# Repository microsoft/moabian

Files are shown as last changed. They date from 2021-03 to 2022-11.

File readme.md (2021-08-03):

# Welcome to Project Moab

Project Moab is an open source ball balancing robot built to demonstrate the end-to-end Microsoft Project Bonsai Platform, a low-code AI platform for building autonomous systems.

If you have the hardware kit, you can find all the setup documentation in the [Wiki](https://github.com/microsoft/moabian/wiki).

You can find an introduction to Autonomous systems and an overview of the Project Bonsai platform [here](https://innovation.microsoft.com/en-us/exploring-autonomous-systems).

For step-by-step tutorials of how to train a brain to balance a ball on Moab, visit the [Project Moab Website](https://microsoft.github.io/moab/).

Simulation is a huge component of Project Bonsai. You can find the python simulator for Project Moab [here](https://github.com/microsoft/moabsim-py). This is also where you can find the inkling files for the Project Moab tutorials.

There is also a MathWorks Project Moab simulation. You can find the Simulink and Simscape Multibody model [here](https://github.com/microsoft/bonsai-simulink/tree/main/samples/moab). Connecting this simulation to Project Bonsai requires the [Microsoft Project Bonsai Simulink Toolbox](https://www.mathworks.com/matlabcentral/fileexchange/75512-microsoft-project-bonsai-simulink-toolbox).

## Microsoft Open Source Code of Conduct

This project has adopted the [Microsoft Open Source Code of Conduct](https://opensource.microsoft.com/codeofconduct/).
For more information see the [Code of Conduct FAQ](https://opensource.microsoft.com/codeofconduct/faq/) or
contact [opencode@microsoft.com](mailto:opencode@microsoft.com)
with any additional questions or comments.

https://opensource.microsoft.com/codeofconduct

## Trademark Notice

Trademarks This project may contain trademarks or logos for projects,
products, or services. Authorized use of Microsoft trademarks or logos
is subject to and must follow Microsoft's Trademark & Brand Guidelines.
Use of Microsoft trademarks or logos in modified versions of this
project must not cause confusion or imply Microsoft sponsorship. Any use
of third-party trademarks or logos are subject to those third-party's
policies.

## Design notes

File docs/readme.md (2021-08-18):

# Getting started with Project Moab

### Power on

Connect Moab to an electrical outlet using the provided power supply.
The bot will automatically boot and display “PROJECT MOAB” when booting.
This can take up to a minute if Moab is not connected to internet. 

### Balance a ball

1. **Joystick Mode**

   Navigate to and select "JOYSTICK" mode by presssing the joystick. The plate will
   rise up and now you can manually control the pitch and roll of the
   plate using the joystick. Place the ping pong ball on the plate and
   try balancing the ball manually! 

   To exit Joystick mode, select the menu button next to the joystick.

2. **PID Mode**

    This is a PID (Proportional, Integral, Derivative) controller
    that balance the ball at the center of the plate. This controller
    works by minimizing the error between the actual ball position and
    velocity, and the desired ball position and velocity. This type of
    controller is the most commonly found in industrial control
    applications. This controller has been tuned specifially for the ping pong ball.

    Move the joystick down and select "PID" mode. Place the orange
    ping pong ball on the plate and watch Moab automatically balance
    the ball. Try disturbing the ball by poking it or blowing on it and
    watch Moab return the ball to the center.

    If Moab is unable to balance a ball or making erratic movements, see [Troubleshooting](https://github.com/microsoft/moabian/blob/main/docs/troubleshooting.md).

    To exit PID mode, select the menu button next to the joystick.

3. **Brain Mode**

    This is a brain that has been trained using the Bonsai platform. The
    brain is a neural network that has been trained using two goals:
    prevent the ball from falling off the plate, and balance the ball at
    the center of the plate. For details of how this brain was trained, see [Moab Tutorial 2](https://microsoft.github.io/moab/tutorials/2-robustness/index.html).

     Move the joystick down and select "BRAIN" mode. Place the orange
     ping pong ball on the plate and watch Moab automatically balance
     the ball. Try disturbing the ball by poking it or blowing on it and
     watch Moab return the ball to the center.

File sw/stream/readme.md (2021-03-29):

pip3 install --user requirements.txt
python3 app.py

-or-

gunicorn --threads 5 --works 1 --bind 0.0.0.0:8080 app:app

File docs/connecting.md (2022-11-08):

# Connecting to Moab

To deploy your own brain on Moab, you will need to connect to it on your
local network. For the initial setup, we recommend using an ethernet
cable to connect your Moab to your local network. If you are unable to
connect to your network with an ethernet cable you can do so using WiFi.
To configure the WiFi on your Moab, you will need an HDMI monitor and
USB keyboard.

## Option 1: Connecting with an ethernet cable

### Required Materials

- Ethernet cable (to connect Moab to your local network)

Connect one end of an ethernet cable to your Moab and the other end to
your router.

## Option 2: Connecting with an HDMI monitor and USB keyboard

### Required Materials

- HDMI Monitor
- USB Keyboard

1. Connect Moab to a monitor using an HDMI cable.

2. Connect Moab to a USB keyboard.

3. When prompted for the moab login, use "pi" and "raspberry":

    login: pi
    password: raspberry

4. Follow the instructions in the next section to enable the WiFi.

## Enable WiFi (required for Option 2)

1. Type `sudo raspi-config`, and hit enter to open the Raspberry Pi
Software Configuration Tool.

    >sudo raspi-config

2. If prompted, select your country from the list. You can type the
first letter of your country as a short cut.

3. Select **1 System Options**.

4. Select **S1 Wireless LAN**.

5. Enter your WiFi network name.

6. Enter your WiFi password.

7. Select **Finish**.

## SSH into Moab

There are multiple methods to SSH into Moab. We provide instructions for
using Visual Studio Code.

#### SSH into Moab using Visual Studio Code

1. Open Visual Studio Code. If you don't have it you can download it for
free [here](https://code.visualstudio.com/).

2. Add the extension **Remote - SSH**, if you don't already have it.
Click on the Extensions icon on the left, and search "Remote - ssh" as
shown in the following example. Click **Install**.

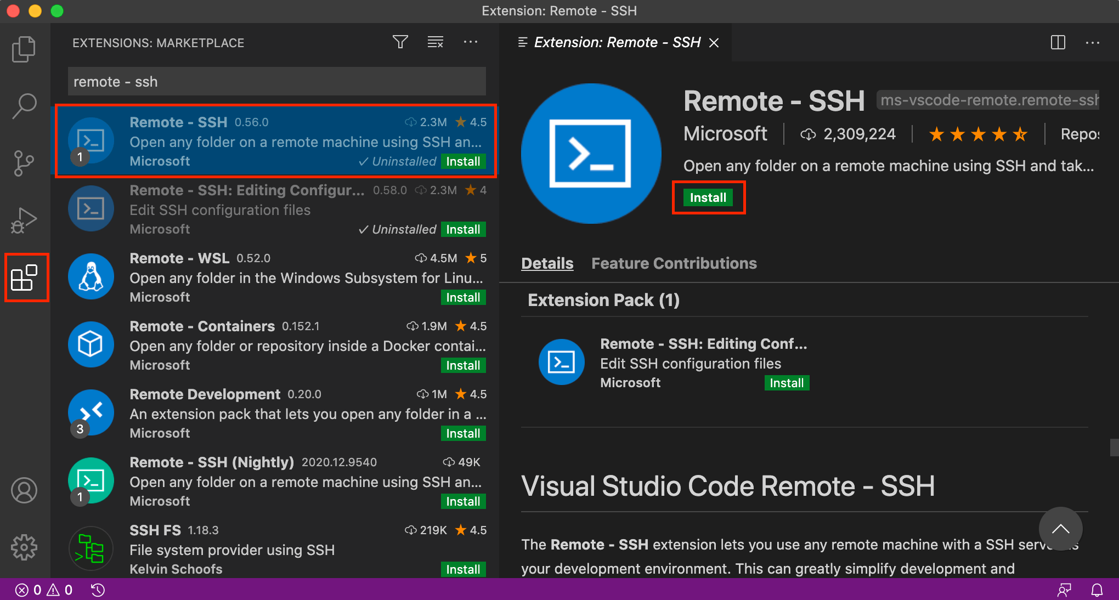
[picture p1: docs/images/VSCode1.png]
VSCode1
   

3. Add a new SSH host. Open the Command Palette through the **View**
menu as shown in the following screenshot:

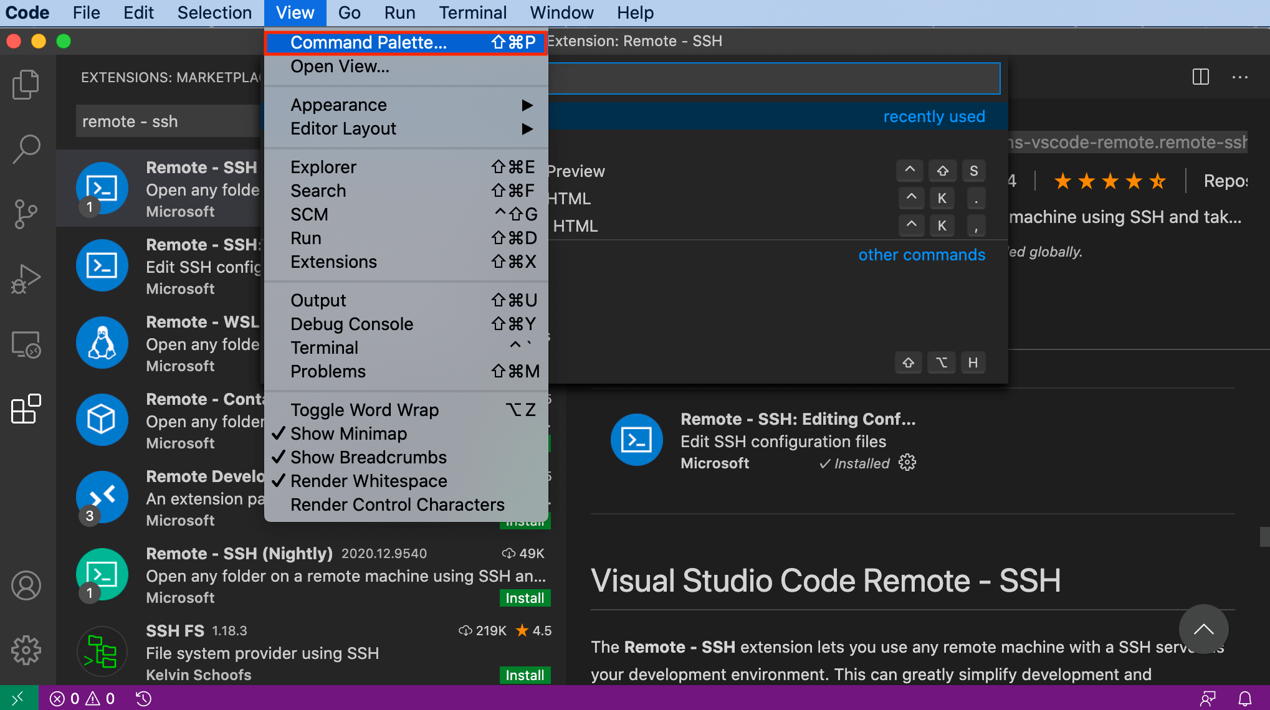
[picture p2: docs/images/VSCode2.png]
VSCode2
    

    Search for the command **Remote-SSH: Add New SSH Host...** as shown
    in the following screenshot:

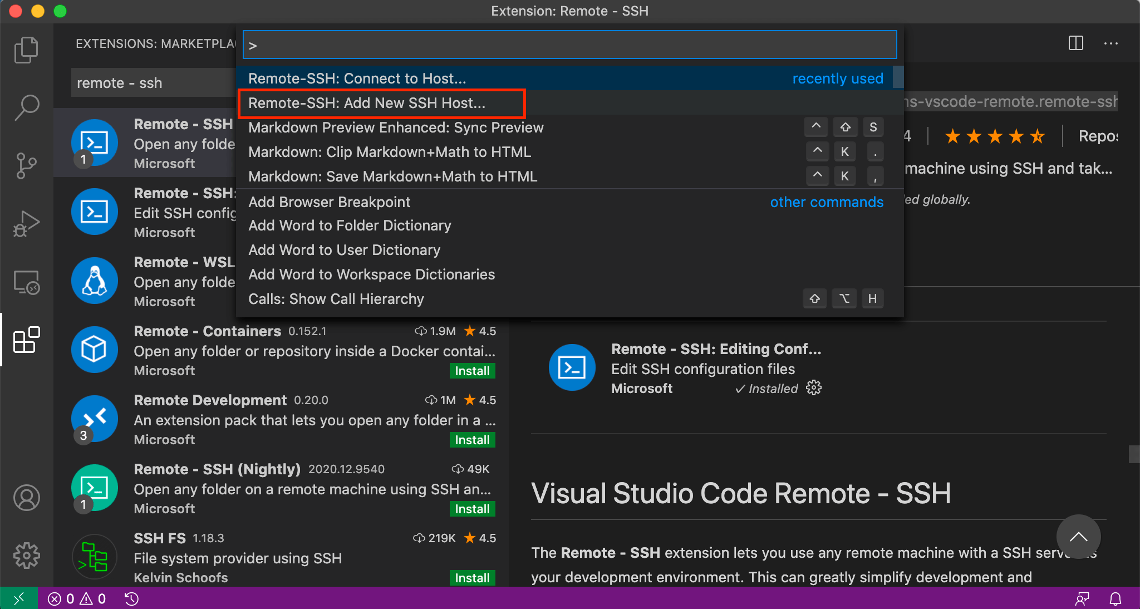
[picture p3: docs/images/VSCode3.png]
VSCode3
    

    Follow the prompts to create or update an SSH configuration file and
    add a new SSH Host. 

    Use the user and host/IP `pi@moab.local` when prompted:

    >pi@moab.local
    
   Note: If you can't connect with `pi@moab.local`, try `pi@moab`. If that doesn't work, then try the following:
   
   * On your Moab device, use the thumbstick to scroll down to `BOT INFO`.
   * Click the thumbstick to select the menu option. The Moab device IP ADDRESS will be displayed.
   * Try `pi@<IP ADDRESS FROM BOT INFO>` Replace `<IP ADDRESS FROM BOT INFO>` with the IP ADDRESS from the Moab device.   

    Use the password `raspberry` when prompted.

    >raspberry

4. Connect to SSH Host. Search for and select the command **Remote-SSH:
Connect to Host...**. Follow the prompts. When you have successfully
connected, you will will see "**SSH: moab.local**" in the bottom left
corner of the VS Code window as shown in the following screenshot:

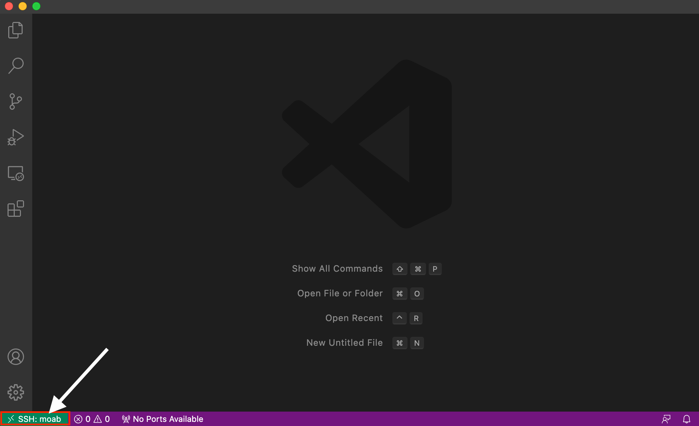
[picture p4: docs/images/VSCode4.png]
VSCode4


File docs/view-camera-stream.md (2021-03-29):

# View Camera Stream

You can view the camera stream in a web browser from http://moab.local. The stream is only active when Moab is in the following Modes: JOYSTICK, PID, BRAIN1, or custom brains.

If the link above is not working, try by simply using the Moab IP address.

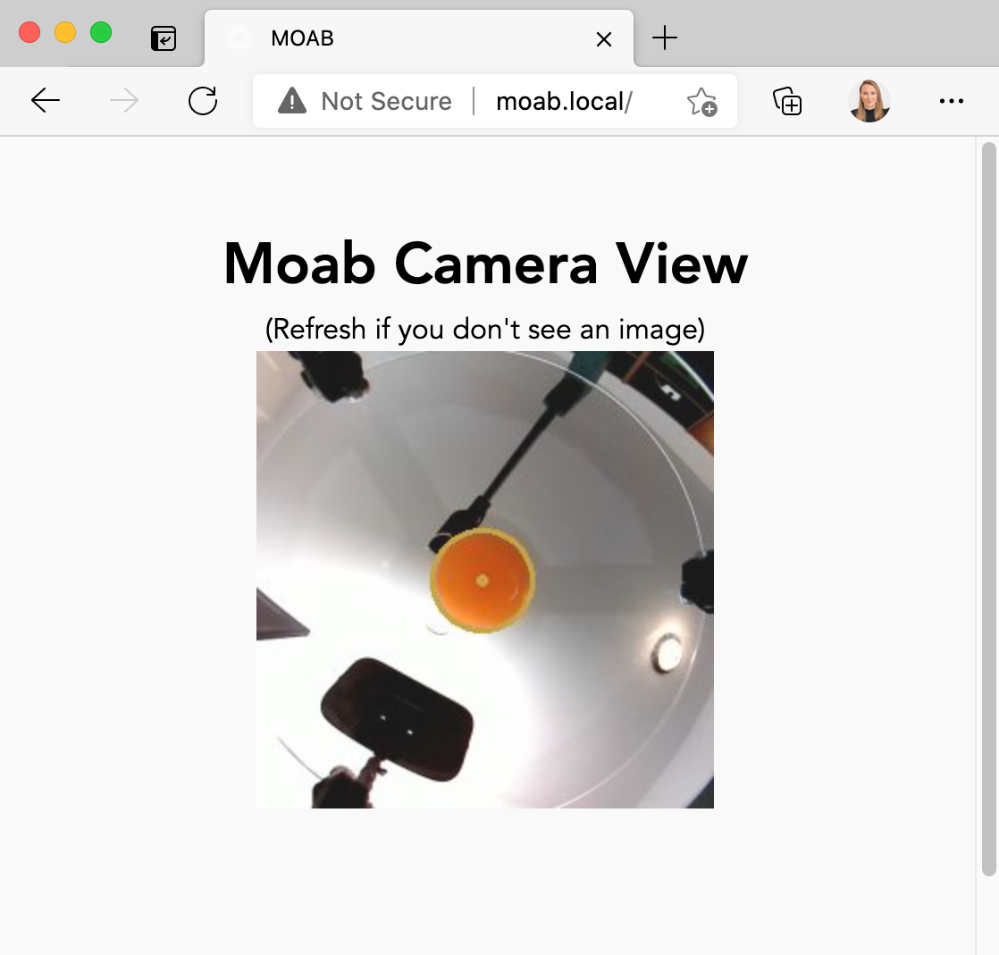
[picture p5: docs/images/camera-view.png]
camera-view


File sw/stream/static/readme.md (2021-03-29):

# Quick html web server on Raspberry Pi

I wanted to test these pages in three browsers (Edge, Firefox and
Safari) without hitting refresh, i.e., auto-load when the static folder
changes.

Install node via npm to get the `live-server` app:

```bash
curl -o- https://raw.githubusercontent.com/nvm-sh/nvm/v0.35.3/install.sh | bash
nvm install node
npm i -g live-server
live-server

```
Now in your browsers, open one of these:

```
http://moab:8080/grid.html
http://moab.local:8080/grid.html
```

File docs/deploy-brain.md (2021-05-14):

# Deploy a Brain on Moab

### Retrieve ACR credentials

1. Copy/paste the following docker login statement into your text
editor: *(You’ll paste your credentials from your Container Registry
into it during later steps)*

    > `docker login <YOUR LOGIN SERVER> -u <YOUR USERNAME> -p '<YOUR
    > PASSWORD>' `

    DeployBrain1

2. Login to [https://portal.azure.com](https://portal.azure.com)

3. Go to your **Bonsai workspace**

4. Click on **Registry** in upper right corner to go to the **Container
Registry** page, as in the following screenshot:  

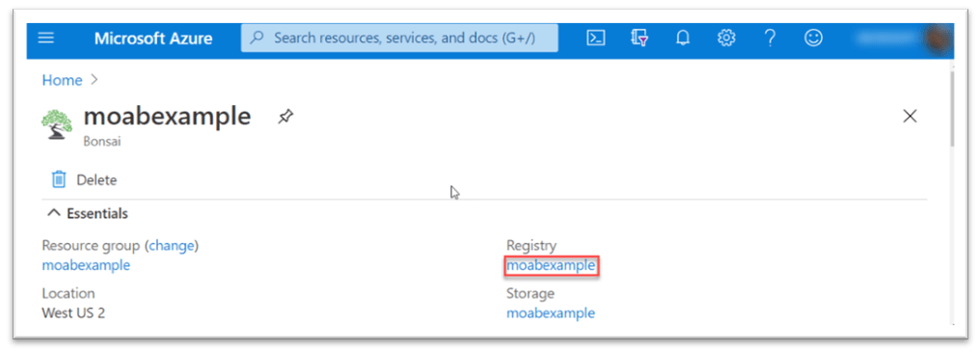
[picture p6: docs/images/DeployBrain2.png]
DeployBrain2
   

5. On the **Container Registry** page, in the **Settings** section
(left-hand menu), click the **Access Keys** page link, as in the
following screenshot:

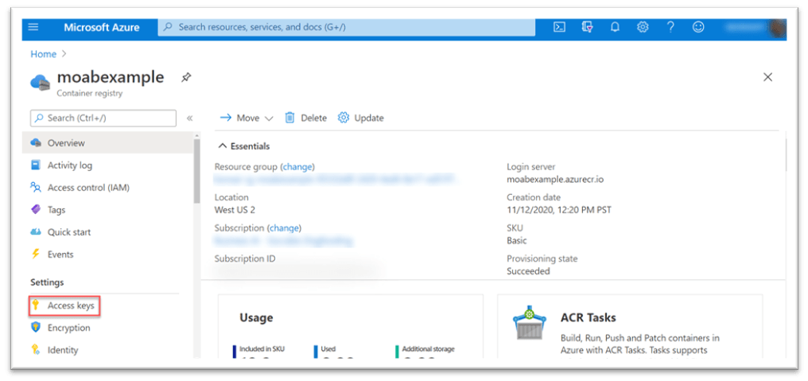
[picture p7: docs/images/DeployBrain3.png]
DeployBrain3
   

6. In the **Access Keys** page, copy/paste the **Login server** name,
**Username**, and **Password** into a text editor, as in the following
screenshot:

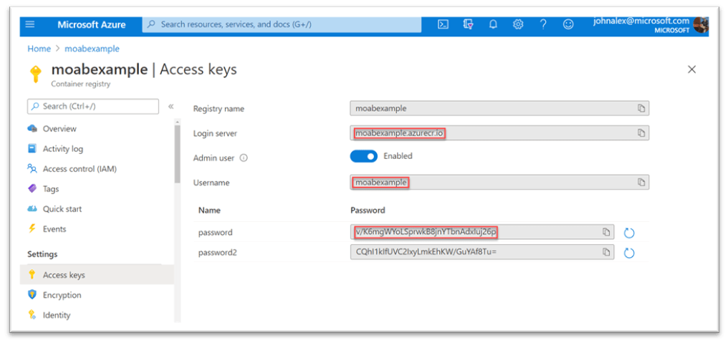
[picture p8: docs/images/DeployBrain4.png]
DeployBrain4
   

7. In your text editor, replace the `<values>` in the docker login
statement using the fields you copied (keep the single quotes around
password), as in the following example:

   DeployBrain5

### Login to ACR from Moab

1. Open Visual Studio Code. If you have not yet already, SSH into Moab
following the previous instructions.

2. Open a new terminal window. You can do this by selecting "**New
Terminal**" from the terminal window as shown in the screenshot below:

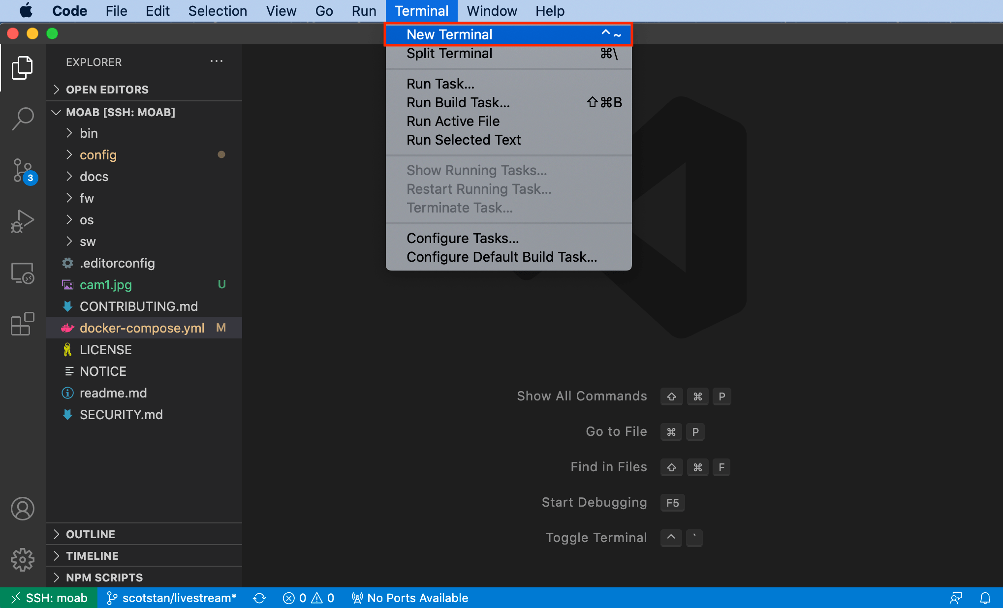
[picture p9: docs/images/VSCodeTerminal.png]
VSCodeTerminal
    

3.	Copy/Paste or type the previously completed **docker login**
statement in to the terminal and hit enter. 

3. Type `cd moab`, and hit enter, to go to the moab directory.

4. Paste the **docker pull** command from your text editor and hit
enter.

5. After the docker pull completes, type `docker images` and hit the
enter to see the exported brain image in the list.

### Edit the docker-compose.yml file

1. Select"**Open Folder**" as shown in the following screenshot.
Alternatively, you can select **File** --> **Open**

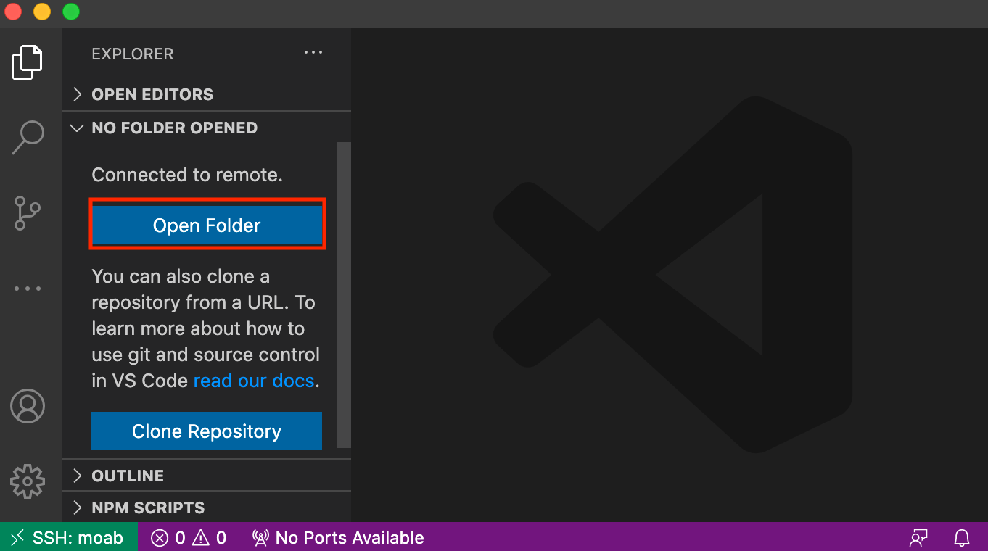
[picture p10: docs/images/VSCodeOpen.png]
VSCodeOpen
    

    Select **moab** from the dropdown or type the file path
    `/home/pi/moab/` and select **OK**.

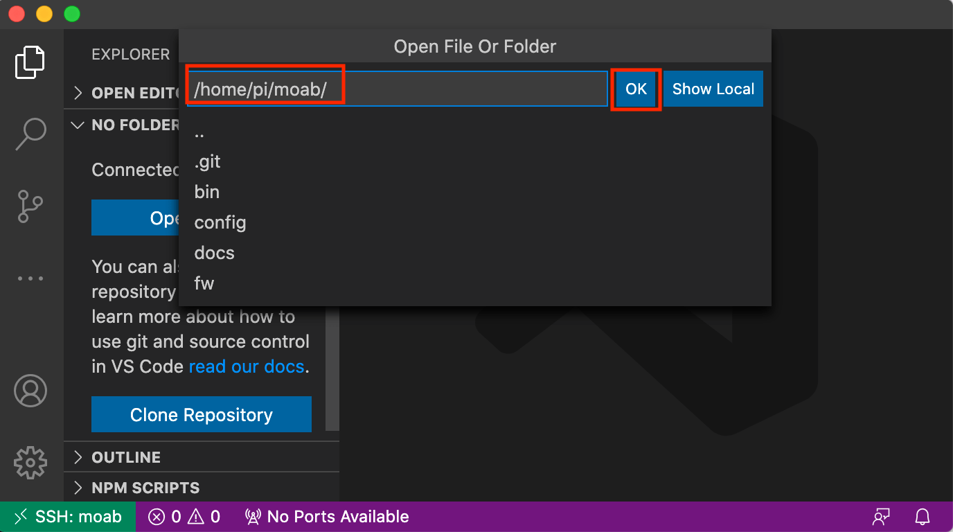
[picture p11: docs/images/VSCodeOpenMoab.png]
VSCodeOpenMoab
    

1. Open the **docker-compose.yml** file by selecting in from the menu on
the left.

1. Uncomment lines 10 - 14 for a new custom brain section.  
You can modify the container name on line 12 for a friendly name that will be displayed on the menu. If the `container name:` is not present, Moab will parse image name and display it on the menu instead.  

1. On line 11, copy/paste the image name of your exported brain (everything after the words `docker pull`) from the text editor, as in the following screenshots: 

   DC1

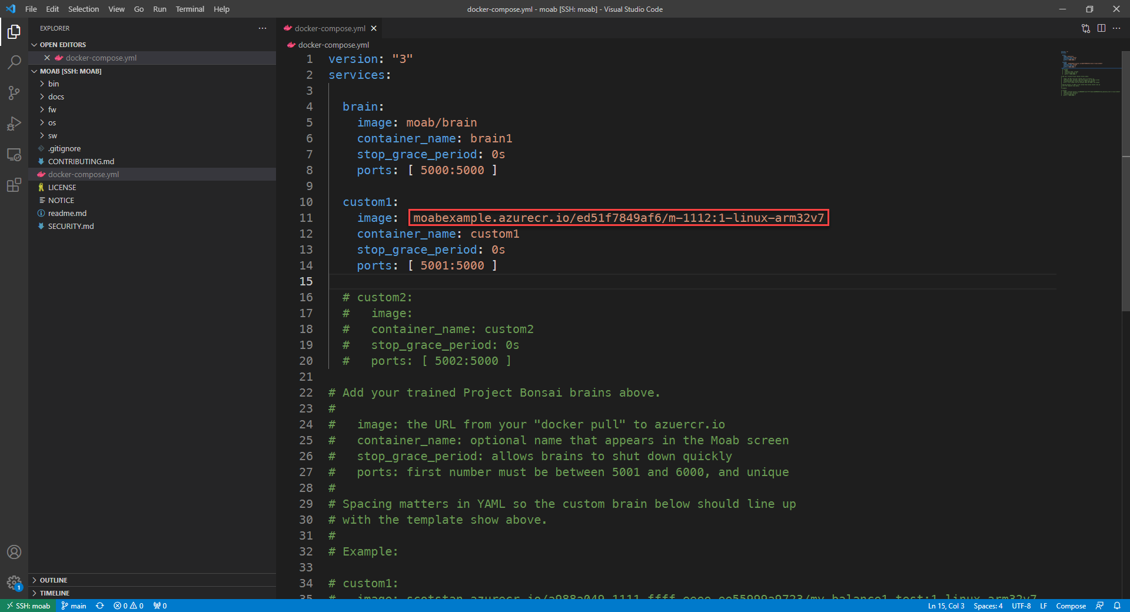
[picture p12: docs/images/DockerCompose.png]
DockerCompose
    

1. Save the file.

### Restart your Moab and test your deployed brain

1. In the terminal, type `sudo reboot now` and hit enter to restart the Moab control service.

1. Test your new exported brain on your Moab hardware by selecting your custom brain name on your Moab menu (don’t forget your ping pong ball!).

[!NOTE]>
>For additional brains,after doing your docker pull,  copy/paste lines 10-14, copy/paste your image name,  change "custom1:" and the 'container name:' to something unique and iterate the port.

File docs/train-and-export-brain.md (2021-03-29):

# Train and Export a Brain

## Train a brain

If you have not trained a brain already, please follow [Project Moab
tutorial](https://microsoft.github.io/moab/tutorials/) 1, 2 or 3 to
train a brain. 

**Prerequisites**: To complete the tutorials, you must have a Bonsai
workspace provisioned on Azure. If you do not have one, follow the
[account setup
guide](https://docs.microsoft.com/en-us/bonsai/guides/account-setup).

## Export a brain for deployment

1. In the Bonsai UI, Click on “**Export brain**” button in the Train tab
for your trained brain, as in the following screenshot:  

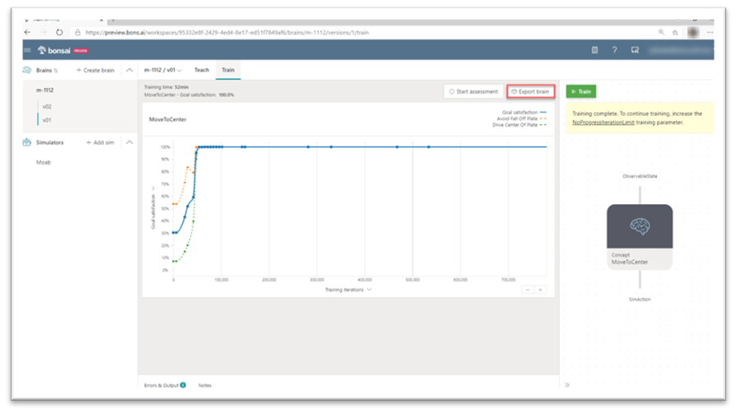
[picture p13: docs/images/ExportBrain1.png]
ExportBrain1
    

2. In the “**Export brain**” pop-up, under “**Processor architecture**”,
select “Linux” and “**ARM32V7**”, as in the following screenshot:  

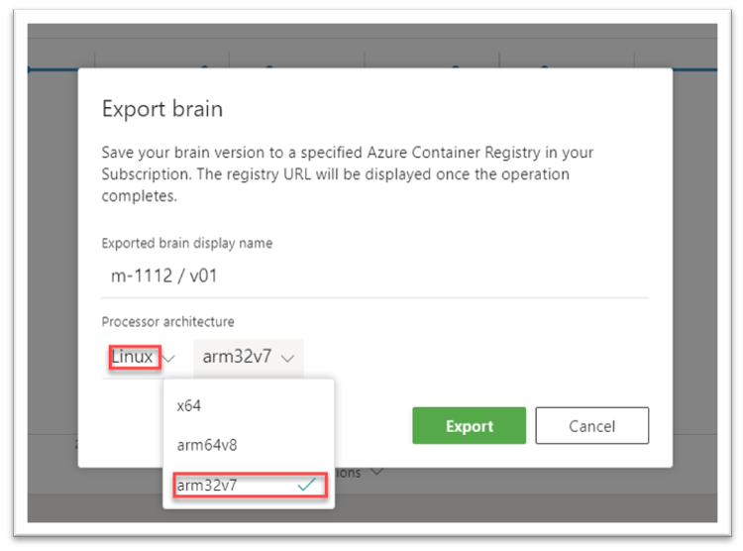
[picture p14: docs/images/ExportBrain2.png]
ExportBrain2
    

3. Press the “**Export**” button, as in the following screenshot:

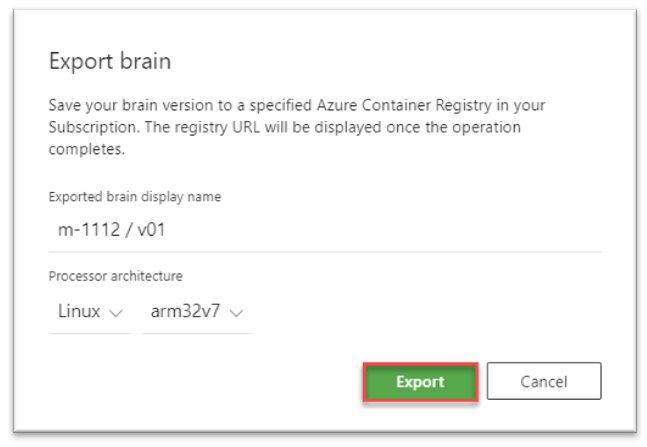
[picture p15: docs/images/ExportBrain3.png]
ExportBrain3
    

4. The brain version will appear in the **Exported Brains** list on the
left-hand side of the UI with an “**Exporting brain…**” status, as in
the following screenshot:

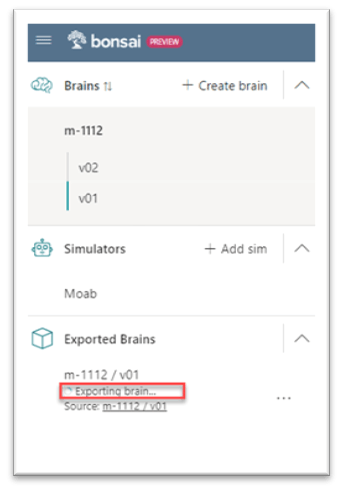
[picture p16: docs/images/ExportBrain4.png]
ExportBrain4
    

5. After your brain is exported, the “**Brain export complete!**” pop-up
will appear, as in the following screenshot:

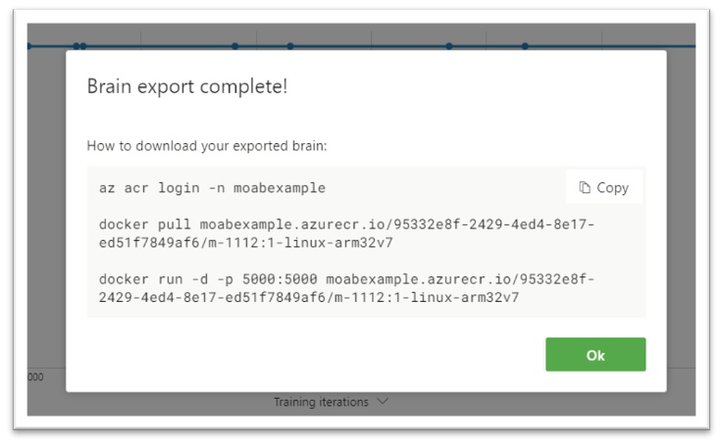
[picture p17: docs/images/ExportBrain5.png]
ExportBrain5
    

    If the “**Export brain**” pop-up doesn’t appear after the export
    completes, click on the ellipsis (…) and click on “**View download
    info**” , as in the following screenshot:

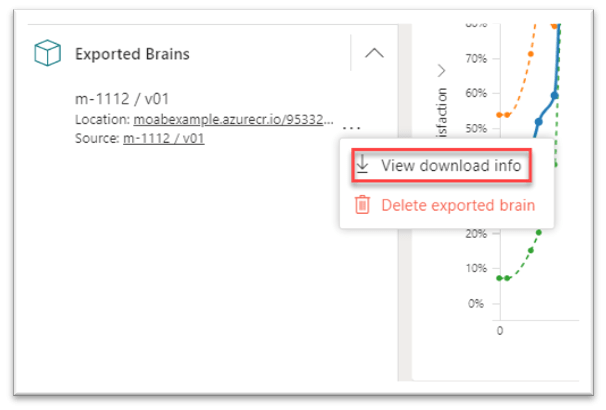
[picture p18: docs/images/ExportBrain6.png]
ExportBrain6
    

    The “**Download exported brain**” pop-up will appear. It has the
    same download information.

6. Copy the **docker pull** command (middle line) from the exported
brain pop up, as in the following screenshot: 

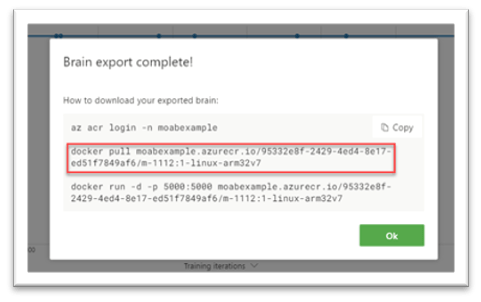
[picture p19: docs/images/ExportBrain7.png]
ExportBrain7
    

7. Open your favorite text editor and copy/paste the **docker pull**
command.  

    ExportBrain8

    You’ll use it to pull down your exported brain into your Moab during
    later steps.

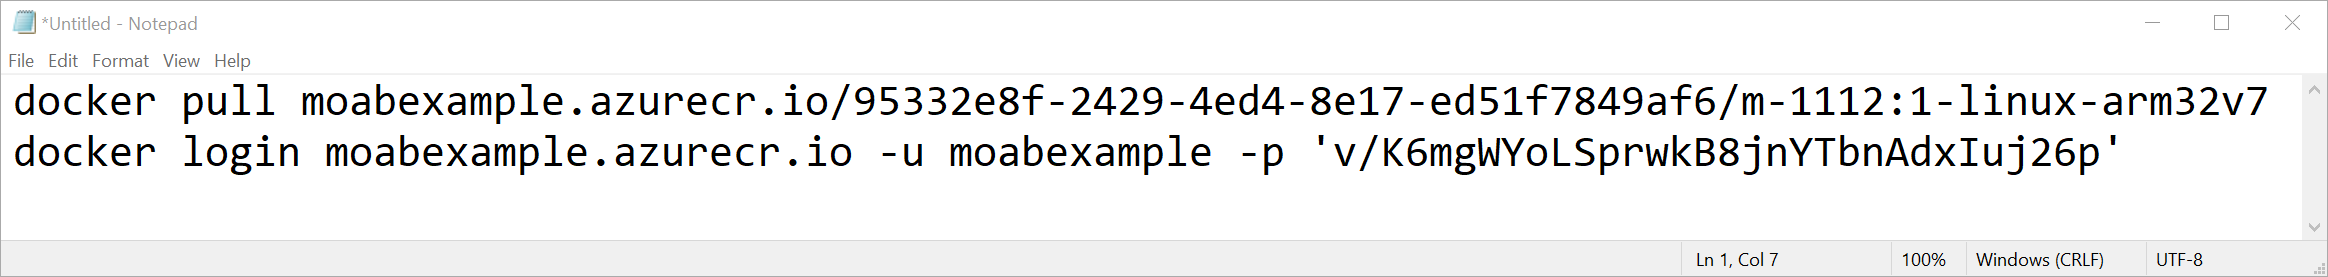
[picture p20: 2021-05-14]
docs/DeployBrain5.png

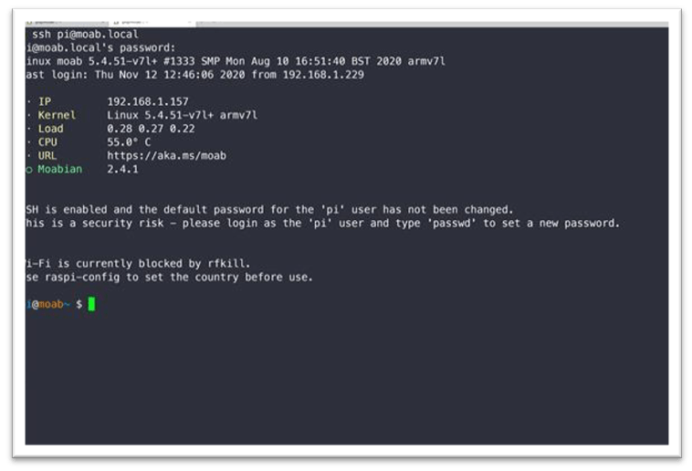
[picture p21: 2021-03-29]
docs/images/ssh.png

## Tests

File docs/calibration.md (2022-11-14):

# Moab Calibration

Moab calibration consists of 3 components:

- Ball Hue: This is the color hue used by OpenCV to detect the ball. The default calibration is for the orange ball but the hue can change based on the lighting. If your Moab is having difficulty balancing the ball, try recalibrating to ensure proper ball detection.

- Ball Position: Each Moab is slightly different due to tolerances in the parts so this calibration determines the X and Y offsets to the center of the ball on the plate.

- Servo Offset: These are the servo offsets that determine a level plate. Since there are three servos, there are three offset values.

## Ball Hue and Position Calibration

These calibration values are updated in one step. It is important to perform this step as soon as you setup your Moab or if you move it to a new location since it is affected by the lighting.

1. In the menu, navigate to and select CALIBRATION. Follow the prompts on the Moab screen. If calibration is successful, the Ball Hue value will be displayed.

You can always view the hue value on your Moab by navigating to and selecting HUE INFO.

## Servo Offset (plate level) calibration

The servo offset calibration is a bit more advanced and is only necessary to do if your Moab is having trouble balancing the ball or the plate visibly needs to be leveled. It is important to complete the Ball Hue and Position calibration step before following this procedure. [Connecting](https://github.com/microsoft/moabian/blob/docs-v3-updates/docs/connecting.md) to your Moab is a prerequisite to this procedure.

1. To check the level of the plate, navigate to and select JOYSTICK. Place the ball on the center of the plate and observe where it rolls off the plate. If the ball does not roll, but stays in place, your plate is level and you do not need to complete this calibration.

2. SSH into Moab (see instructions in previous section)

3. Navigate to the moab/sw folder (`cd moab/sw`) and run the plate level  program (`p level_plate.py`). The three numbers in the program correspond to the three servo offsets. Use increase or decrease the offsets, the `u` and `j` keys for the first offset, the `i` and `k` keys for the second, and the `o` and `l` keys for the thrid. As you ajust the offsets you should see the plate move.

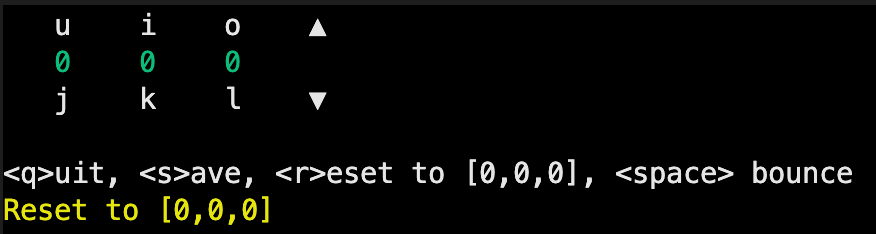
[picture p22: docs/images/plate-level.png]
plate-level


4. Update the servo offset values until the plate is level. You can verify the plate is level by placing the ball on the plate and ensuring it does not move. Save the offsets with the `s` key and then close the level plate program with the `q` key.

You can always view the servo offset values on your Moab by navigating to and selecting HUE INFO.

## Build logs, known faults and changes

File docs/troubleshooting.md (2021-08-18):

# Troubleshooting

## Unable to balance ball

If your Moab is not able to balance a ball in PID or BRAIN1 mode, we recommend the following troubleshooting steps:

1. Check your lighting situation. Are there any objects or lights in the room that Moab could be mistaking for orange ping pong balls? You can check by viewing the camera stream. Follow the directions [here](https://github.com/microsoft/moabian/blob/docs-update/docs/view-camera-stream.md). 
       
     If this is the case try moving Moab to another location, blocking the lights, or changing the lighting situation.

2. Calibrate the ball hue and position. These instructions can be found on the [Calibration](https://github.com/microsoft/moabian/blob/docs-v3-updates/docs/calibration.md) page. If calibrating the ball hue and position does not solve the problem, complete the Servo Offset calibration as well.

3. If your Moab is still having trouble after calibrating, try using different colored balls, such as [these](https://www.amazon.com/STIGA-Assorted-Multicolor-Recreational-Quality-Regulation/dp/B000GF6030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).

3. If your Moab is still unable to balance a ball after following the steps above, please contact us for troubleshooting assistance.
       
## Hardware Issues

If you are experiencing any hardware issues, such as bot not turning on, see the [Troublshooting Manual](https://github.com/microsoft/moabian/blob/main/docs/MoabTroubleshootingDoc.pdf).

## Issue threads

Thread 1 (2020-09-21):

Power-off button not lowering plate and clearing OLED

scotstan, 2020-09-21:
I can see using `journalctl -f` an error thrown when calling `oled 0 0` for permissions (needs sudo).

Closed 2020-09-22.

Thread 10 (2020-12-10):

Color calibration for non-orange balls doesn't work

scotstan, 2020-12-10:

Closed 2021-03-18.

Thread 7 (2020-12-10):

Fine tune the 3 arms for perfect level

scotstan, 2020-12-10:
While the robots three arms are calibrated during assembly, it's possible that the servos drift as the tolerance is a rough 0.5º. When the plate is in manual mode, it should be level to your desk. If not, we are building a small command-line tool to find the right +/- degree offsets to fine tune the bot.

scotstan, 2020-12-14:
Merged to v2.5

Closed 2020-12-14.

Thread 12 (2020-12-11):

Show a QR code to Moab to set wifi

scotstan, 2020-12-11:
If you don't have an ethernet cable **and** you don't have an HDMI monitor + keyboard, there's no way to configure Moab (easily) to put it on your wifi network.

An idea came up where one could "show" Moab's camera a QR code with wifi details.

keenbrowne, 2020-12-11:
There are other projects that have tried to do this for linux: https://github.com/kokoye2007/wifi-qr for example.  This site has more of a description of what's involved in the process: https://qifi.org/

scotstan, 2020-12-11:
Got the code working after installing a few libraries:

```
sudo apt-get install libzbar0
pip3 install --user pyzbar imutils
```

And with this snippet:
```
from imutils.video import VideoStream
from pyzbar import pyzbar
import imutils
import time
import cv2

vs = VideoStream(usePiCamera=True).start() # For Pi Camera
time.sleep(0.25)

while True:
    frame = vs.read()
    frame = imutils.resize(frame, width=400)
    barcodes = pyzbar.decode(frame)
    for barcode in barcodes:
        print("found one")
        (x, y, w, h) = barcode.rect
        cv2.rectangle(frame, (x, y), (x + w, y + h), (0, 0, 255), 2)
        barcodeData = barcode.data.decode("utf-8")
        barcodeType = barcode.type
        text = "{} ({})".format(barcodeData, barcodeType)
        print(text)

vs.stop()
```

scotstan, 2020-12-11:
Data would go in `/etc/wpa_supplicant/wpa_supplicant.conf`

scotstan, 2020-12-12:
Link for above:
https://circuitdigest.com/microcontroller-projects/qr-code-scanner-using-raspberry-pi-and-opencv

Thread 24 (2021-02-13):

docker-compose.yml version number invalid

scotstan, 2021-02-13:
Report from Muntazir Mehdi reporting:

```
ERROR: The Compose file './docker-compose.yml' is invalid because:

Invalid top-level property "iversion". Valid top-level sections for this Compose file are: version, services, networks, volumes, secrets, configs, and extensions starting with "x-".

You might be seeing this error because you're using the wrong Compose file version. Either specify a supported version (e.g "2.2" or "3.3") and place your service definitions under the `services` key, or omit the `version` key and place your service definitions at the root of the file to use version 1.

For more on the Compose file format versions, see https://docs.docker.com/compose/compose-file/
```

## To track this down, I'll be asking for a screenshot of the following commands:

```
splash
docker-compose --version
docker --version
head -5 ~/moab/docker-compose.yml
```

My moab output:

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

munti, 2021-02-14:
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

munti, 2021-02-14:
· IP         192.168.1.21
 · Kernel     Linux 5.4.51-v7l+ armv7l
 · Load       0.04 0.01 0.00
 · CPU        59.9° C
 · URL        https://aka.ms/moab
 ○ Moabian    2.4.1

scotstan, 2021-02-14:
You have the letter `i` as the first character in the file. That might be a `vim` side effect (insert mode). Maybe try deleting that?

```
% vim moab/docker-compose.yml
x
[shift-ZZ]
% up
```

munti, 2021-02-15:
I removed the letter "i". that was a good catch. I have a different problem, where when I try to do cd moab, cd moab
-bash: cd: moab: No such file or directory. Can you please post the link for a fully functional  docker-compose.yml file, so i could verify if it is correct.

munti, 2021-02-15:
also, i noticed that the moab is not on the latest version - is there a way to update it.

scotstan, 2021-02-16:
Once you log in via ssh:

```
cd moab
cat docker-compose.yml
```

If you don't have a moab folder, then ping me through email and we'll debug.

The `docker-compose.yml` file you need is here in the root of the repo:
https://github.com/microsoft/moabian/blob/main/docker-compose.yml

You have the only released & supported version, 2.4.1. We have a new branch v3 that we're testing this week for release ASAP. We'll be updating the readme, tags and main branch when released. There's a wiki for v3 migration, but I don't recommend it yet.

Closing this particular issue as resolved (the 'i' issue).

Closed 2021-02-16.

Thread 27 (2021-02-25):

Use AI to locate the ball

scotstan, 2021-02-25:
Great suggestion from @mikeestee

1. Train an ONYX/TF model to turn "ball in video frame" into a "normalized x/y" coord.
2. Update the simulator to render the ball as a video frame, instead of synthesizing it directly from the physics.
3. Import that and then combine it with one or more concepts for controlling the servos
4. Export to moab.
5. ???
6. Profit

We use openCV computer vision algorithms to find the dominate hue of the center pixel space during calibration. Then use that color for the Hough circle detection algorithm. It does mean you have to recalibrate for different color balls, and the detection is sensitive to changing ambient lights (dark room vs sunny).

Would require the synthesis of simulated data and/or lots of real frames of data. Since we have labeled data *now* from ideal conditions (i.e., we can easily save videos with meta-data of circles where the ball is), we can get a good start.

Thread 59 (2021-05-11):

Camera view http://moab.local is too small

scotstan, 2021-05-11:
Capture is 256x256 which is pretty small. Let's double it to 512x512 in the view (not the capture).

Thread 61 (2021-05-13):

New brains aren't recognized after bot reset

JRAlexander, 2021-05-13:
When deploying a custom brain, the new brain shows in the menu but throws a "brain not found" error after bot reset.
Current workaround: tap power button or use sudo reboot 0.

Closed 2022-12-19.

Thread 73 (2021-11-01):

Velocity calculation is not accurate after ball dissapears from frame

polzounov, 2021-11-01:
Whenever the ball falls off the plate and the ball is no longer detected, the calculation for the velocity becomes inaccurate and needs to be reset.

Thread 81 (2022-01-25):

Consider calling DELETE when the ball is no longer seen

scotstan, 2022-01-25:
After a ball falls off the plate (terminal condition), then if you pick it up and put it back on the plate, then we should reset the echo state memory.

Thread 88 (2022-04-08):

Plan for BullsEye changes

JRAlexander, 2022-04-08:
https://www.raspberrypi.com/news/raspberry-pi-bullseye-update-april-2022/#comments

scotstan, 2022-06-22:
- [] upgrade `splash` so show version
- [] test from clean Bullseye image
- [] strategy for default pi username and password
- [] test upgrade path from Buster (v10)
- [] moby certificates might be expired?

scotstan, 2022-06-22:
`opencv` install from `os/setup` fails with this error:

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

scotstan, 2022-06-22:
Seeing this in `dmesg` boot log:

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

Rebooting after setup found `/dev/ttyAMA1`

scotstan, 2022-06-22:
Manual setup worked. Now encountering camera issues (joystick crashes). Issues in `diagnose`

https://www.tomshardware.com/how-to/use-raspberry-pi-camera-with-bullseye

scotstan, 2022-06-22:
No `picamera` support re:
https://www.raspberrypi.com/news/bullseye-camera-system/

scotstan, 2022-06-26:
Bullseye uses **Python 3.9.2** and ["we won't change that".](https://www.raspberrypi.com/news/raspberry-pi-bullseye-update-april-2022/#comment-1582645)

scotstan, 2022-06-26:
`ctrl-alt-t` opens a terminal window in the wizard environment. From there `sudo cancel-rename pi` will restore original pi user (this is per the comments from above).

Also the base OS is built with pi-gen according to `/etc/rpi-issue`

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

scotstan, 2022-06-26:
Notes from one of the lead devs on updating from buster to bullseye:

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

scotstan, 2022-06-26:
The Moab wide-angle camera is "OV5647"

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

| For a CM4 on Waveshare Nano carrier board, I had to follow [these steps](https://www.waveshare.com/wiki/CM4-IO-BASE-B) to enable the camera.

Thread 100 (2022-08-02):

Live streaming moab camera failing

scotstan, 2022-08-02:
Repro, this fails:

% python -c "import flask"

Reason: dependency on jinja2 removed
https://stackoverflow.com/questions/71718167/importerror-cannot-import-name-escape-from-jinja2

Currently triaging.

Closed 2022-09-02.

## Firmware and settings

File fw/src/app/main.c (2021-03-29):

// Copyright (c) Microsoft Corporation.
// Licensed under the MIT License.
#include "headers.h"
#include "app_version.h"
#include "plate.h"
#include "spi.h"
#include "display.h"

LOG_MODULE_REGISTER(main);

void main(void)
{
    pi_to_hat_t rx;
    u8_t last_control;

    u8_t mb_idx = 0;
    char message_buffer[255];

    float servo1_pos, servo2_pos, servo3_pos;
    u16_t servo1_pos_centi_deg, servo2_pos_centi_deg, servo3_pos_centi_deg;

    LOG_INF("Version %s", log_strdup(APP_SEMVER));
    LOG_INF("Word Size %d. pi_to_hat_t %d", sizeof(void *), sizeof(pi_to_hat_t));

    plate_init();

    while (true)
    {
        // process incoming SPI msgs
        if (wait_for_pi_message(&rx, K_FOREVER) == 0)
        {
            last_control = rx.control;

            switch (rx.control)
            {
                case COPY_STRING:
                    if (mb_idx == 0)
                        memset(message_buffer, 0, sizeof(message_buffer));
                    if (mb_idx < 240) {
                        memcpy(&message_buffer[mb_idx], rx.data.characters, 7);
                        mb_idx += 7;
                    }
                    else
                        LOG_ERR("String too long to display. Max length is 240 bytes.");
                    break;

                case DISPLAY_BIG_TEXT_ICON:
                    message_buffer[mb_idx] = '\0';  // Add a termination char just in case
                    mb_idx = 0;
                    LOG_INF("0x%02x (%d) TEXT=%s", rx.control, (u8_t) rx.data.icon, log_strdup(message_buffer));
                    display_big_text_icon(message_buffer, (disp_icon_t) rx.data.icon);
                    break;

                case DISPLAY_BIG_TEXT:
                    message_buffer[mb_idx] = '\0';  // Add a termination char just in case
                    mb_idx = 0;
                    LOG_INF("0x%02x TEXT=%s", rx.control, log_strdup(message_buffer));
                    display_big_text(message_buffer);
                    break;

                case DISPLAY_SMALL_TEXT:
                    message_buffer[mb_idx] = '\0';  // Add a termination char just in case
                    mb_idx = 0;
                    LOG_INF("0x%02x text=%s", rx.control, log_strdup(message_buffer));
                    display_small_text(message_buffer);
                    break;

                case DISPLAY_POWER_SYMBOL:
                    message_buffer[mb_idx] = '\0';  // Add a termination char just in case
                    mb_idx = 0;
                    LOG_INF("0x%02x (%d) TEXT=%s", rx.control, (u8_t) rx.data.icon, log_strdup(message_buffer));
                    display_big_text_power_icon(message_buffer, (disp_power_icon_t) rx.data.icon);
                    break;

                case SERVO_ENABLE:
                    LOG_INF("0x%02x servos: on", rx.control);
                    plate_servo_enable(true);
                    break;

                case SERVO_DISABLE: 
                    LOG_INF("0x%02x servos: off", rx.control);
                    plate_servo_enable(false);
                    break;

                case SET_SERVOS:
                    // Convert bytes to uint16
                    servo1_pos_centi_deg = ((rx.data.servo1_pos_centi_deg_high_byte << 8) + rx.data.servo1_pos_centi_deg_low_byte);
                    servo2_pos_centi_deg = ((rx.data.servo2_pos_centi_deg_high_byte << 8) + rx.data.servo2_pos_centi_deg_low_byte);
                    servo3_pos_centi_deg = ((rx.data.servo3_pos_centi_deg_high_byte << 8) + rx.data.servo3_pos_centi_deg_low_byte);
                    // Convert from hundredths of a degree to degrees
                    servo1_pos = ((float) servo1_pos_centi_deg) / 100.0;
                    servo2_pos = ((float) servo2_pos_centi_deg) / 100.0;
                    servo3_pos = ((float) servo3_pos_centi_deg) / 100.0;

                    plate_servo_update_position(0, servo1_pos);
                    plate_servo_update_position(1, servo2_pos);
                    plate_servo_update_position(2, servo3_pos);
                    break;

                case NOOP:
                    break;

                default:
                    LOG_ERR("Bad control byte: %0x2x. Prior was: %0x2x", rx.control, last_control);
                    break;
            }
        }
    }
}

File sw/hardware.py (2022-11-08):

# Copyright (c) Microsoft Corporation.
# Licensed under the MIT License.

import os
import time
import json
import numpy as np

from settings import get_settings
from detector import hsv_detector
from typing import Tuple, Optional
from camera import OpenCVCameraSensor
from hat import Hat, Buttons, Icon, PowerIcon


def plate_angles_to_servo_positions(
    pitch: float,
    roll: float,
    arm_len: float = 55.0,
    side_len: float = 170.87,
    pivot_height: float = 80.0,
    angle_max: float = 160,
    angle_min: float = 90,
) -> Tuple[float, float, float]:
    servo_angles = [0.0, 0.0, 0.0]

    z1 = pivot_height + np.sin(np.radians(roll)) * (side_len / np.sqrt(3))
    r = pivot_height - np.sin(np.radians(roll)) * (side_len / (2 * np.sqrt(3)))
    z2 = r + np.sin(np.radians(-pitch)) * (side_len / 2)
    z3 = r - np.sin(np.radians(-pitch)) * (side_len / 2)

    if z1 > 2 * arm_len:
        z1 = 2 * arm_len
    if z2 > 2 * arm_len:
        z2 = 2 * arm_len
    if z3 > 2 * arm_len:
        z3 = 2 * arm_len

    servo_angles[0] = 180 - (np.degrees(np.arcsin(z1 / (2 * arm_len))))
    servo_angles[1] = 180 - (np.degrees(np.arcsin(z2 / (2 * arm_len))))
    servo_angles[2] = 180 - (np.degrees(np.arcsin(z3 / (2 * arm_len))))

    servo_angles = np.clip(servo_angles, angle_min, angle_max)
    return servo_angles


class MoabHardware:
    def __init__(
        self,
        frequency=30,
        debug=False,
        verbose=0,
        calibration_file="bot.json",
    ):
        self.debug = debug
        self.verbose = verbose
        self.frequency = frequency

        self.hat = Hat(debug=debug, verbose=verbose)
        self.hat.open()
        self.camera = OpenCVCameraSensor(frequency=frequency)
        self.detector = hsv_detector(debug=debug)

        # Set the calibration
        self.calibration_file = calibration_file
        self.reset_calibration()

    def __enter__(self):
        self.camera.start()
        return self

    def __exit__(self, type, value, traceback):
        self.go_down()
        self.hat.disable_servos()
        self.hat.display_power_symbol("TO WAKE", PowerIcon.POWER)
        self.hat.close()
        self.camera.stop()

    def __repr__(self):
        return self.__str__()

    def __str__(self):
        return (
            f"serial number: {self.serial_number}, "
            f"hue: {self.ball_hue}, "
            f"color: {self.ball_color}, "
            f"plate offsets: {self.plate_offsets}, "
            f"servo offsets: {self.servo_offsets}"
        )

    def reset_calibration(self, calibration_file=None):
        # Use default if not defined
        calibration_file = calibration_file or self.calibration_file
        settings_dict = get_settings(calibration_file)

        self.servo_offsets = settings_dict["servo_offsets"]
        self.plate_offsets = settings_dict["plate_offsets"]
        self.hue = settings_dict["ball_hue"]

    def go_up(self):
        # Set the plate to its hover position, experimentally found to be 150
        self.set_servos(150, 150, 150)
        time.sleep(0.200)  # Give enough time for the action before turning off servos

    def go_down(self):
        # Set the plate to its lowest position, experimentally found to be 155
        self.set_servos(155, 155, 155)
        time.sleep(0.200)  # Give enough time for the action before turning off servos

    def get_buttons(self):
        # Get the buttons after doing a noop (ensure the buttons are up to date)
        self.hat.noop()
        return self.hat.get_buttons()

    def enable_servos(self):
        self.hat.enable_servos()

    def disable_servos(self):
        self.hat.disable_servos()

    def set_servos(self, s1, s2, s3):
        # Note the indexing offset
        o1, o2, o3 = self.servo_offsets
        self.hat.set_servos((s1 + o1, s2 + o2, s3 + o3))

    def display(
        self,
        text: Optional[str] = None,
        icon: Optional[str] = None,
        scrolling: bool = False,
    ):
        # Optionally display the controller active text
        if icon and text:
            if scrolling:
                raise ValueError("Cannot display scrolling screen with an icon")
            self.hat.display_string_icon(text, icon)
        elif text:
            if scrolling:
                self.hat.display_long_string(text)
            else:
                self.hat.display_string(text)

    def set_angles(self, pitch, roll):
        s1, s2, s3 = plate_angles_to_servo_positions(pitch, roll)
        self.set_servos(s1, s2, s3)

    def step(self, pitch, roll) -> Buttons:
        self.set_angles(pitch, roll)
        frame, elapsed_time = self.camera()
        buttons = self.hat.get_buttons()
        ball_detected, (ball_center, ball_radius) = self.detector(
            frame, hue=self.hue
        )
        return ball_center, ball_detected, buttons

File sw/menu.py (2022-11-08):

#!/usr/bin/env python3

# Copyright (c) Microsoft Corporation.
# Licensed under the MIT License.

import os
import sys
import time
import yaml
import json
import click
import docker
import procid
import logging
import subprocess

from hat import Icon
from enum import Enum
from env import MoabEnv
from functools import partial
from log_csv import log_decorator
from settings import get_settings
from dataclasses import dataclass
from calibrate import calibrate_controller
from typing import Callable, Any, Union, Optional, List
from procid import setup_signal_handlers, stop_doppelgänger
from info_screen import (
    info_screen_controller,
    info_config_controller,
    options_controller,
)
from controllers import (
    pid_controller,
    zero_controller,
    brain_controller,
    joystick_controller,
    dump_ball_controller,
    kiosk_mode_decorator,
    BrainNotFound,
)

LOG = logging.getLogger(__name__)


@dataclass
class MenuOption:
    name: str
    closure: Callable
    kwargs: dict
    # Some menu options are controllers (run a control loop), others are simply
    # blocking functions that return on menu press. These other functions are
    # for anything that does something to the bot (displaying info to the screen,
    # doing a calibration, running git pull, etc.)
    is_controller: bool = True
    decorators: Optional[List[Callable]] = None  # List of functions to decorate
    require_servos: bool = True  # To not turn on servos unnecessarily


class MenuState(Enum):
    first_level = 1  # In the main menu screen (selecting beteween menu options)
    second_level = 2  # Inside a controller or 'modal' (running the fn from MenuOption)


def squash_small_angles(controller_fn, min_angle=1.0):
    """
    Decorates a controller that sets actions smaller than a certain angle to 0.
    """
    # Acts like a normal controller function
    def decorated_controller(state):
        action, info = controller_fn(state)  # The actual controller
        (pitch, roll) = action

        if abs(pitch) < min_angle:
            pitch = 0
        if abs(roll) < min_angle:
            roll = 0

        action = (pitch, roll)
        return (action), info

    return decorated_controller


def build_menu(env, log_on, logfile, kiosk, kiosk_timeout, kiosk_clock_position):
    log_csv = lambda fn: log_decorator(fn, logfile)

    # fmt: off
    top_menu = [
        MenuOption(
            name="Calibrate",
            closure=calibrate_controller,
            kwargs={
                "env": env,
                "pid_fn": pid_controller(),
                "calibration_file": "bot.json",
            },
            is_controller=False,
        ),
        MenuOption(
            name="Joystick",
            closure=joystick_controller,
            kwargs={},
            decorators=[squash_small_angles, log_csv] if log_on else [squash_small_angles],
        ),
        MenuOption(
            name="PID",
            closure=pid_controller,
            kwargs={},
            decorators=[log_csv] if log_on else None,
        ),
    ]
    # fmt: on

    # Parse the docker-compose.yml file for a list of brains
    middle_menu = []
    # Parse brains from docker ps and add to middle_menu
    for brain_image in docker.ps():
        if kiosk:  # Kiosk-ify brains if kiosk mode is enabled
            m = MenuOption(
                name=brain_image.short_name,
                closure=kiosk_mode_decorator,
                kwargs={
                    "env": env,
                    "timeout": kiosk_timeout,
                    "dump_location_clock_hand": kiosk_clock_position,
                    "controller": brain_controller,
                    "controller_kwargs": {
                        "port": brain_image.port, "alert_fn": alert_callback
                    },
                },
                decorators=[log_csv] if log_on else None,
            )
        else:
            m = MenuOption(
                name=brain_image.short_name,
                closure=brain_controller,
                kwargs={"port": brain_image.port, "alert_fn": alert_callback},
                decorators=[log_csv] if log_on else None,
            )
        middle_menu.append(m)

    bottom_menu = [
        MenuOption(
            name="Hue Info",
            closure=info_config_controller,
            kwargs={"env": env},
            is_controller=False,
            require_servos=False,
        ),
        MenuOption(
            name="Bot Info",
            closure=info_screen_controller,
            kwargs={"env": env},
            is_controller=False,
            require_servos=False,
        ),
        MenuOption(
            name="Settings",
            closure=options_controller,
            kwargs={"env": env},
            is_controller=False,
            require_servos=False,
        ),
    ]

    return top_menu + middle_menu + bottom_menu


def kiosk_mode(env, dump_location_clock_hand):
    # Convert from hour hand location to degrees
    dump_angle = ((-dump_location_clock_hand + 3) * (360 / 12)) % 360
    dump_ball_fn = dump_ball_controller(angle=dump_angle, tilt_angle=5)
    zero_fn = zero_controller()

    # Dump the ball for 1 second
    for _ in range(env.frequency * 1):
        action, _ = dump_ball_fn((state, detected, buttons))
        state, detected, buttons = env.step(action)
        time.sleep(1 / env.frequency)

        if buttons.menu_button:
            return (state, detected, buttons), True

    # Level the plate
    action, _ = zero_fn((state, detected, buttons))
    state, detected, buttons = env.step(action)

    # Disable servos
    env.hardware.disable_servos()
    time.sleep(1 / env.frequency)

    # Wait until the ball is detected again for 3 consecutive frames
    detected_count = 0
    detected = False
    while detected_count < 3:
        action, _ = zero_fn((state, detected, buttons))
        state, detected, buttons = env.step(action)
        time.sleep(1 / env.frequency)

        if detected:
            detected_count += 1
        else:
            detected_count = 0

        if buttons.menu_button:
            env.hardware.enable_servos()
            return (state, detected, buttons), True

    # Re-enable servos
    env.hardware.enable_servos()
    time.sleep(1 / env.frequency)

    return (state, detected, buttons), False


# color list: https://github.com/pallets/click/blob/master/examples/colors/colors.py
out = partial(click.secho, bold=False, err=True)
err = partial(click.secho, fg="red", err=True)


def alert_callback(is_error):
    if is_error:
        err("Brain predict error")


def _handle_debug(ctx, param, debug):
    log_level = logging.DEBUG if debug else logging.INFO
    logging.basicConfig(
        format="[%(asctime)s] %(levelname)s: %(message)s",
        level=log_level,
    )
    return debug
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

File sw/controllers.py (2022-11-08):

# Copyright (c) Microsoft Corporation.
# Licensed under the MIT License.

import sys
import time
import requests
import numpy as np
import logging as log

from enum import IntEnum
from env import MoabEnv
from common import Vector2


class BrainNotFound(Exception):
    pass


# Controllers ------------------------------------------------------------------
def pid_controller(
    Kp=75,  # Proportional coefficient
    Ki=0.5,  # Integral coefficient
    Kd=45,  # Derivative coefficient
    max_angle=22,
    **kwargs,
):
    def next_action(state):
        env_state, ball_detected, buttons = state
        x, y, vel_x, vel_y, sum_x, sum_y = env_state

        if ball_detected:
            action_x = Kp * x + Ki * sum_x + Kd * vel_x
            action_y = Kp * y + Ki * sum_y + Kd * vel_y
            action_x = np.clip(action_x, -max_angle, max_angle)
            action_y = np.clip(action_y, -max_angle, max_angle)

            action = Vector2(action_x, action_y)

        else:
            # Move plate back to flat
            action = Vector2(0, 0)

        return action, {}

    return next_action


def joystick_controller(max_angle=16, **kwargs):
    def next_action(state):
        env_state, ball_detected, buttons = state
        action = Vector2(-buttons.joy_x, -buttons.joy_y)
        return action * max_angle, {}

    return next_action


def dump_ball_controller(angle=90, tilt_angle=16, **kwargs):
    """Dump the ball towards angle."""

    def next_action(state):
        env_state, ball_detected, buttons = state
        a = -tilt_angle * np.cos(np.radians(angle))
        b = -tilt_angle * np.sin(np.radians(angle))
        action = Vector2(a, b)
        return action, {}

    return next_action


def zero_controller(**kwargs):
    def next_action(state):
        return Vector2(0.0, 0.0), {}

    return next_action


def brain_controller(
    max_angle=22,
    port=5555,
    client_id=123,
    alert_fn=None,
    **kwargs,
):
    """
    This class interfaces with an HTTP server running locally.
    It passes the current hardware state and gets new plate
    angles in return.
    The hardware state is unprojected from camera pixel space
    back to real space by using the calculated plate surface plane.

    Note: Still use v1 endpoint even if it's a v2 brain because on every new
    creation of a brain controller we still call DELETE on the v2 brain
    endpoint. This way we don't need to know information about what the trained
    brain was called to navigate the json response.
    """
    # Reset memory if a v2 brain
    status = requests.delete(f"http://localhost:{port}/v2/clients/{client_id}")
    version = 2 if status.status_code == 204 else 1

    if version == 1:
        prediction_url = f"http://localhost:{port}/v1/prediction"
    elif version == 2:
        prediction_url = f"http://localhost:{port}/v2/clients/{client_id}/predict"
    else:
        raise ValueError("Brain version `{self.version}` is not supported.")

    def next_action_v1(state):
        env_state, ball_detected, buttons = state
        x, y, vel_x, vel_y, sum_x, sum_y = env_state

        observables = {
            "ball_x": x,
            "ball_y": y,
            "ball_vel_x": vel_x,
            "ball_vel_y": vel_y,
        }

        action = Vector2(0, 0)  # Action is 0,0 if not detected or brain didn't work
        info = {"status": 400, "resp": ""}
        if ball_detected:

            # Trap on GET failures so we can restart the brain without
            # bringing down this run loop. Plate will default to level
            # when it loses the connection.
            try:
                # Get action from brain
                response = requests.get(prediction_url, json=observables)
                info = {"status": response.status_code, "resp": response.json()}

                if response.ok:
                    pitch = info["resp"]["input_pitch"]
                    roll = info["resp"]["input_roll"]

                    # Scale and clip
                    pitch = np.clip(pitch * max_angle, -max_angle, max_angle)
                    roll = np.clip(roll * max_angle, -max_angle, max_angle)

                    # To match how the old brain works (only integer plate angles)
                    pitch, roll = int(pitch), int(roll)
                    action = Vector2(-roll, pitch)

            except requests.exceptions.ConnectionError as e:
                print(f"No brain listening on port: {port}", file=sys.stderr)
                raise BrainNotFound
            except Exception as e:
                print(f"Brain exception: {e}")
        return action, info

    def next_action_v2(state):
        env_state, ball_detected, buttons = state
        x, y, vel_x, vel_y, sum_x, sum_y = env_state

        observables = {
            "state": {
                "ball_x": x,
                "ball_y": y,
                "ball_vel_x": vel_x,
                "ball_vel_y": vel_y,
            }
        }

        action = Vector2(0, 0)  # Action is 0,0 if not detected or brain didn't work
        info = {"status": 400, "resp": ""}
        if ball_detected:

            # Trap on GET failures so we can restart the brain without
            # bringing down this run loop. Plate will default to level
            # when it loses the connection.
            try:
                # Get action from brain
                response = requests.post(prediction_url, json=observables)
                info = {"status": response.status_code, "resp": response.json()}

                if response.ok:
                    concepts = info["resp"]["concepts"]
                    concept_name = list(concepts.keys())[0]  # Just use first concept
                    pitch = concepts[concept_name]["action"]["input_pitch"]
                    roll = concepts[concept_name]["action"]["input_roll"]

                    # Scale and clip
                    pitch = np.clip(pitch * max_angle, -max_angle, max_angle)
                    roll = np.clip(roll * max_angle, -max_angle, max_angle)

                    # To match how the old brain works (only integer plate angles)
                    pitch, roll = int(pitch), int(roll)
                    action = Vector2(-roll, pitch)

            except requests.exceptions.ConnectionError as e:
                print(f"No brain listening on port: {port}", file=sys.stderr)
                raise BrainNotFound
            except Exception as e:
                print(f"Brain exception: {e}")
        return action, info

    if version == 1:
        return next_action_v1
    elif version == 2:
        return next_action_v2
    else:
        raise ValueError("Brain version `{self.version}` is not supported.")
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

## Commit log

2020-09-22 2.4.1 (#3)
    * Send SIGINT to docker for quick shutdown
    The --signal=2 flag corresponds to SIGINT, a signal the main.py
    controller is listening for. When received it lowers the plate and
    clears the OLED screen.
    The default signal is SIGKILL wasn't being caught, resulting in the
    controller quitting without lowering the plate.
    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
2020-12-14 Setup 2.5 adds /etc/environment
    This adds two new environment variables:
    MOABIAN=2.5
    MOABDIR=/home/pi/moab
    Available for scripts and passing to docker-compose for volume mounting.
2020-12-14 New: offset tool to add +/- values to each servo
    Although the servo arms come adjusted and calibrated during assembly,
    we've found that local level variations (i.e., your table isn't actually
    level) or tolerance stacking requires small tweaks for your Moab.
    It's helpful to think of the 3 servos as positions on a clock dial. With the
    joystick positioned nearest you, at the 6 o'clock position, the servos are:
    1: 12 o'clock (top) position
    2: 8 o'clock
    3: 4 o'clock
    Typical usage is a manual, iterative process:
    ```
    % down # first stop moab controller
    % offset # show current offsets (from ~/moab/config/calibration.json)
    % offset -s 5 0 0 # Say the 12 o'c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
2020-12-14 Live stream the camera to http://moab.local:5000
    For this commit, only bare-metal dev works:
    (In window 1)
    cd ~/moab/sw
    sudo python3 main.py -t 1 --device=manual
    (In window 2)
    cd ~/moab/sw/stream
    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
2020-12-15 New: Bot Info menu item (#17)
    * Swap order of these install steps
    * Wire up the info screen device
    * New "Bot Info" menu item on Moab
    Shows the IP address and firmware version.
2020-12-23 Bot info and OLED makefile fixes
    * oled, pymoab and moab setup
    * Upgrade pip and remove old packages
    * Promote libmoab v2 as the new shared library
    * Missing equals sign in requirements version
    * Fix pymoab and cmoab library installs
    * Wrong dependency
    * Enable camera frame saving for streaming
2020-12-23 Add OpenCV streaming camera option (#19)
    * Adding OpenCV option and jpeg quality
    * Add OpenCV streaming option
    Allows us to view the camera if Moab control isn't running. Early
    version of crosshairs / reticle.
2021-01-15 Add opencv streaming (#20)
    * WIP: adding opencv.html page
    * Use stacked grid cells for reticle
    * Setup notes for node on RPI
    * Test CSS grid page
    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
2021-01-15 Initial prototype of new firmware
2021-01-15 Switched moab to new interface entirely
2021-01-16 Removed return from spi.writebtyes2
2021-01-16 Added assert that spi is initialized
2021-01-16 Fix spi init
2021-01-22 Hacky fix for interface problems (hat is class, devices have a hat)
2021-01-24 Added prototype of new env arch
2021-01-24 Progress on fixing new arch
    [detector.py, env.py]
2021-01-24 Fixed camera debug bug
    [camera.py]
2021-01-24 Bugfixes and debugging (including proper image rotation)
    [camera.py, common.py, detector.py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]
2021-01-24 Working detector and camera improvements
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2021-02-05 Partial fix to problems in 3.0
    [camera.py, common.py, controllers.py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]
2021-02-05 Remove cropping in camera
2021-02-07 Comment out line so pid works
2021-02-07 Working PID & brain with units of meters
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2021-02-07 Default to pid controller
2021-02-09 Added sleep after setting servos or plate angle
2021-02-09 Let camera frequency handle our timing (it's a blocking call)
2021-02-09 Revert the sleep after sending plate angles/servo positions
    [hat.py]
2021-02-09 Ugly add log to PID
2021-02-10 Added the plate angle to servo position transform
2021-02-10 Switch to derivative instead of hpf
2021-02-11 Partially complete increase servo precision
2021-02-14 Using only set servos now
2021-02-14 Fix axes and remove useless prints
    [controllers.py, hat.py]
2021-02-14 Added back plate angles to hat with a flag
2021-02-15 Switch to huemask from pymoab
2021-02-16 Make /tmp/camera/frame.jpg the default view
2021-02-16 Use xy offset to find center of camera
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2021-02-18 CAL_INSTR seems to trigger a fw bug
    [calibrate.py]
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2021-02-22 Fixed the plate angle to servo transform
    [hat.py]
2021-02-22 Fixed polarity of plate angles
    [controllers.py, hat.py]
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2021-02-22 Didn't actually save env.py after the merge 🤦
    [env.py]
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2021-02-22 fixed the Low pass filter (todo match tau & fc for hpf)
    [common.py]
2021-02-22 Skip stdout hexyl if first byte is noop 0x00
    [hexyl.py]
2021-02-25 Minimal reset and timing
    [hat.py, hexyl.py, run_simple.py]
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2021-03-02 Sync with v.3.0.9 firmware (#28)
    * SPI bus timing bumped from 10k Hz to 100k Hz fixed RX bug
    [common.py, env.py, hat.py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]
2021-03-03 Better text (#30)
    * Send strings to the firmware directly
    * WIP
    * poll to get
    * Must have the last sleep
    * Calibration works for hue and plate offset
    * Typo
    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
2021-03-03 Small improvements and fixes
    [calibrate.py, env.py, hat.py]
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2021-03-08 v3.0.11 alpha
    * Double the streaming image size
    * Set MOABIAN version on install
    * Use click for args and black because
    * Shorten info screen
    * MANUAL to JOYSTICK, CLASSIC to PID
    * Use the new pad 8 byte function
    * Isolate GPIO setup for SIGINT handling
    * Deprecate run.py as entry point
    * Add a nice __repr__ for EnvState
    * No longer need to make some *.py executable
    * Grabbing the GPIO pin forces a firmware reset. This takes at least 1
    second. If the user hits ctrl-c, gracefully handle the exception.
    [common.py, hat.py, hexyl.py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]
2021-03-08 Some Python style and import fixes
    [hat.py, menu.py]
2021-03-09 Lower max_angle to avoid gimbal lock
    [controllers.py]
2021-03-10 Squashed commit of the following:
    commit 4eead6c901da4e1fcb20188592ce33a243868d94
    Author: Scott Stanfield <scott.stanfield@microsoft.com>
    Date: Tue Mar 9 22:04:13 2021 -0800
    Bashrc color prompt included
    commit 3b83d8257498fad19cac588e215998f8a157fb38
    Author: Scott Stanfield <scott.stanfield@microsoft.com>
    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
2021-03-11 New info screen. Web server http://moab.local
    * served on port 80 via nginx proxied to gunicorn -> flask O_o
    * starts on boot
    * moab/sw/menu starts on boot
    * two new info screens
    To stop:
    % sudo systemctl stop moab
    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
2021-03-12 Don't reset controller if it's a controller
    [hat.py, menu.py]
2021-03-12 Fixes from previous merge
    [env.py]
2021-03-15 Firmware source for the Moab Hat
    The Moab Hat uses an STM32 chip to manage:
    = the SPI bus communication to/from the Pi
    = the three servos via PWM
    = the menu and joystick down buttons
    = the joystick x & y position
    = the 128x32 pixel OLED display
    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
2021-03-16 WIP Menu and Icon refresh problem
    [hat.py, info_screen.py, menu.py]
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2021-03-17 Calib (#34)
    * Calibrate returns from menu
    * New default bot.json
2021-03-17 Now bot.json is created on calibrate
    If your lighting is nominal, then the default hue for the shipping
    orange ball of 44° is ok.
2021-03-17 Fix white space and missing colon
    [controllers.py]
2021-03-17 Display x,y offsets instead of servo offsets in info controller
2021-03-18 Fix crash in menu
    [menu.py]
2021-03-19 Pitch roll (#36)
    * plate_angles_to_servo_positions matches physics
    * Show servo postions in hexyl log in degrees
    * Positive and negative values align
    * Drop extra print
    * Skip NOOPs
    [controllers.py, env.py, hat.py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]
2021-03-19 Adjust joystick and servos start off in menu
2021-03-19 No longer turns on and off servos for controllers that don't need it
    [menu.py]
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2021-03-22 Fix bug from prev commit
    [calibrate.py]
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2021-03-22 Verbose flag -vvv and Ball color in stream work
    * calibrated hue value written to /tmp/hue.045.date.jpg
    * detector.py was passing hue/2 to draw_ball
    * verbose flag passed down to tx/hx hexyl
    * ball outline color now matches calibration color
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2021-03-22 Tighten up firmware logs
    [main.c]
2021-03-22 v3.0.21.rc1 (#37)
    * menu.service/menu.py robust to either one running
    * menu.service will restart if crashes (not SIGTERM or SIGINT)
    * menu.py responsible for being a singleton, not hat.py
    * new option: -c / --cont to startup in a specific controller (0-7)
    * pop-up plate if started "normally" to alert user
    * bot console: launches 4 panels in tmux to ease debugging
    * bot csv: tail -f on /tmp/csv.log for debugging
    * calibrated hue value saved in filename to /tmp/hue.045.date.jpg
    * added verbose flag (-v, -vv, -vvv) to throttle TX/RX buffer printing
    * tapping power button will restart menu if it's not running
    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
    [calibrate.py, controllers.py, detector.py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]
2021-03-23 Color codes fatal errors for tracking.
    [hexyl.py]
2021-03-23 Some small fixes to env
    [env.py]
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2021-03-24 Rc3 (#40)
    * Auto-servo calibration
    * Continuously stream after calibration is finished
    * Add hue value to file name
    * Incorrect test for docker
    Since the brains.service starts with forking=true the systemd will look
    like brains are no longer running. The last test catches this issue.
    * New 2up mode for firmware debugging
    * Added test detector that sees the ball going in a circle
    * Bot cli has 2up and 4up features
    * Color codes fatal errors for tracking.
    * Clarify the -v verbose option
    * Remove docker-compose.yml from version control
    The docker-compose startup script in moab/bin/up detects if one is
    missing, and copies the template version from moab/bin/template.yml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
    [calibrate.py, common.py, controllers.py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]
2021-03-24 Hex fatal error just show normal bytes
    [hexyl.py]
2021-03-25 Start to handle condition when brains fail
    [controllers.py, menu.py]
2021-03-25 Boot time down to 25 seconds from 45
    Menu starts after dhcpd.service finishes.
    Side effect:
    - bot info might not have an IP yet
    - docker might not be ready yet
    Both errors are caught with little down-side as the system boots those
    up within another 10 seconds.
    Used `systemd-analyze critical-chain` for analysis
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2021-03-25 Add --reset flag to menu
    Since a tap on the power button will "system restart moab", adding the
    new --reset flag will send a GPIO signal to quickly (0.05 seconds)
    restart the firmware to a known good state.
    Only necessary if menu.service crashes.
    [menu.py]
2021-03-26 3.0.24 RC6 (#44)
    * Fix double servo offset when calling set_angles
    * 4up view shows power and menu log
    * Change power button restart metrics
    * Hue details shows servo offsets instead of xy
    * Shifting responsibility for "TO WAKE"
    * Default web stream to index.html
    * Remove TODOs
    [calibrate.py, controllers.py, detector.py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]
2021-03-28 Docs merge (#45)
    * Integrate config and calibrate docs
    * Remove scratch text
2021-03-29 Added help text for bot reset and bot fw_reset
    [info_screen.py, procid.py]
2021-03-30 SPI CS fix (#49)
    * Critical firmware fix for SPI chip-select conflict
    Raspberry Pi set to controller mode, but so was the FW. This sets the FW
    CS/NSS line back to peripheral mode.
    * Increment version to 3.0.25
    * Move Calibrate to top per instructions
    [menu.py, spi.c]
2021-03-30 v3.0.28 (#51)
    * FW v3.0.28 hardware controls CS line
    * Default GPIO pin 6 to output for FW reset
    [menu.py, spi.c]
2021-03-31 Docs v3 updates (#52)
    * Update readme.md
    * Update troubleshooting.md
    * Update calibration.md
    * Update calibration.md
2021-04-07 v3.0.30 (#54)
    Fixes intermittent firmware crash due to SPI controller/peripheral
    problem. Specifically SPI chip select (CS) isn't working in Zephyr 2.1
    for devices set to peripheral mode, only controller mode.
    So both Raspberry Pi and the STM32 Moab Hat were both asserting the CS
    bus, causing an intermittent and difficult bug to track down.
    [menu.py, spi.c]
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2021-08-11 Use better hue mask params (reduces error rate 2x) (#63)
    [detector.py]
2021-10-19 Remove extra request. Fixes #67 (#68)
    [controllers.py]
2021-10-22 Refactor parts of env.py and hat.py into new hardware.py (#70)
    hardware.py is Moab specific, higher-level abstraction (SPI interface, calibration, camera, HSV detector).
2021-10-22 Use manual exposure for the pi's camera (#72)
    Exposure is now fixed for office use, so the camera doesn't "hunt" for a better one.
    [camera.py]
2022-01-06 Use the v2 api for v2 brains (#80)
    * Use the v2 api but always use first named concept. Moab only has one concept so this is ok. Prevents tight coupling from the Inkling concept name "MoveToCenter".
    * Bump version to 3.1.1
    [controllers.py, menu.py]
2022-05-26 New cli tool `level` for one-time plate calibration & tests restructuring (#91)
    * Update help text
    * Remove unused "tests"
    * Isolate remaining tests into subfolder "tests" (using sys.path append)
    * level_plate.py is a one-time plate level calibration (new utility to find better servo offsets)
    * Fix bot shell to launch firmware shell
    * New: `level` cli for interactive plate calibration
    [common.py, level_plate.py]
2022-06-22 `--no-log` fix (#95)
    * menu.py `--no-log` was ignored due to bug
    * Add `distance` column to log.csv
    * Add OS version to `splash` to prepare for Bullseye upgrade
    * sw/tests use helper parent.py to import parent folder
    [log_csv.py, menu.py]
2022-09-02 Apache mcumgr CLI breaking changes (#107)
    * Apparently go changed how install works
    * Explicit path for mcumgr
    * Will need to run firmware update after reboot
    * Provide default path for `flash` to v3.bin
    * Explicit post setup steps
    * Remove old firmware versions (to save space)
    Current firmware for v3.x will always be v3.bin
2022-10-04 Add files via upload (#111)
    add plate-level picture for wiki
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2022-11-08 Settings (#120)
    * Kiosk mode & servo safety works with bot.json
    * Most settings work in the options menu
2022-11-14 Fixed spelling in calibration.md (#122)
    fixed spelling in calibration.md
2022-12-26 Bump wheel from 0.35.1 to 0.38.1 in /sw/setup
    Bumps [wheel](https://github.com/pypa/wheel) from 0.35.1 to 0.38.1.
    - [Release notes](https://github.com/pypa/wheel/releases)
    - [Changelog](https://github.com/pypa/wheel/blob/main/docs/news.rst)
    - [Commits](https://github.com/pypa/wheel/compare/0.35.1...0.38.1)
    ---
    updated-dependencies:
    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
